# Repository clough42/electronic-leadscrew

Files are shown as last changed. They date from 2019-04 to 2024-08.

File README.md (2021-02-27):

# Clough42 Lathe Electronic Leadscrew Controller

This is the firmware for a lathe electronic leadscrew controller.  The goal is to replace the change
gears or gearbox on a metalworking lathe with a stepper motor controlled electronically based on an encoder on the
lathe spindle.  The electronic controller allows setting different virtual gear ratios for feeds and threading.

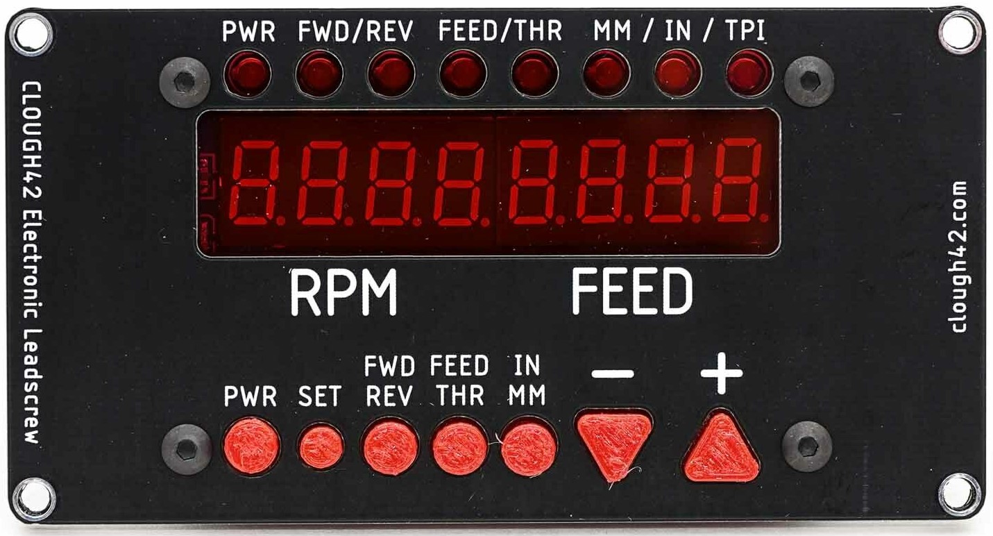
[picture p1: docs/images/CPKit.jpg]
Silkscreened Control Panel


## License and Disclaimer

This software is distributed under the terms of the MIT license.  Read the entire
license statement [here](https://github.com/clough42/electronic-leadscrew/blob/master/LICENSE).

**Machine tools can be dangerous.**  This is especially true of machine tools that can move by themselves
under the control of electronics and software.  You are responsible for your own safety.  Always assume
that something could fail and cause the machine to move unexpectedly.  Keep clear of pinch points and 
be ready to kill the power in an emergency.

## Latest Version

Version 1.4.00 adds the following features and fixes:
* Automatically detect if the ELS hits its max 100KHz step rate and fail safe
* Change the memory map to allow more thread and feed definitions

Version 1.3.01 added the following features and fixes:
* Fix phantom control panel button presses
* Add power button support
* Fix integer overflow for large metric threads
* Prevent mode and direction changes while running
* Smooth tachometer display
* Add support for lathes with separate feed and thread gearing

[DOWNLOAD HERE](https://github.com/clough42/electronic-leadscrew/releases)

## Project Status
Beta.

**NOTE: This is still a work in progress and is subject to change.  Hundreds of people all over the world have purchased parts
and built their own.  That's great!  I have had great success with mine, as have others.  Building an ELS
for your lathe does require require basic electronics and troubleshooting skills, so keep that in mind if you decide to build one
yourself.**

## Documentation
For documentation, please [**VISIT THE PROJECT WIKI**](https://github.com/clough42/electronic-leadscrew/wiki).

## Concept
The project is still in active development.  The current hardware looks like this:
* Use a TI F280049C Piccolo microcontroller on a LaunchXL prototyping board
* Use an inexpensive SPI "LED&Key" import display and keypad for the user interface
* Read the spindle position using a rotary encoder with a 3D-printed gear or belt drive
* Use a standard stepper motor (or servo) and driver on the lathe leadscrew
* Make as few modifications to the lathe as possible:
  * Use the original leadscrew and halfnuts without machining
  * Drive the leadscrew through the factory input shaft
  * Drive the encoder from the factory spindle gear train
  * Make it easy to restore the lathe to the original change gear configuration  

The ELS firmware currently supports the following:
* Feeds in thousandths of an inch per revolution
* Feeds in hundredths of a millimeter per revolution
* Imperial thread pitches (in threads-per-inch)
* Metric thread pitches (in millimeters)
* Imperial and Metric lead screws
* Support for powering down the leadscrew while leaving the tachometer active
* Tachometer averaging (stabilization)

Items on the short list for future development:
* Support for dual-shaft lathes that have different drive ratios for feeding and threading
* Leadscrew speed limit warnings

## Possible Future Goals
While this project is starting out as a simple gearbox replacement, some features seem attractive, even for
that simple case:
* Threading/feeding up to a hard shoulder with automatic stop
* Automatic recall and resync with hybrid threads (e.g. metric threads on an imperial leadscrew)

## Non-Goals
This is not a CNC project.  The goal is not to control the lathe automatically, but rather to transparently
replace the lathe change gears or quick-change gearbox with an electronic virtual gearbox that can be quickly
set to almost any ratio.  The lathe will continue to operate normally, with the operator closing and opening
the half-nuts to control feeding and threading.

## Hardware Configuration
If you want to get this running on your own LaunchXL-F280049C board, here are the settings you will need.
See the documentation at the link above for more details.

### Physical Switches
The LaunchXL-F280049C has a number of switches on the board to configure the GPIO and peripheral signal routing.
This provides lots of flexibility for different uses of the board, but it means that you will have to change
some of the switches from their defaults in order to use the GPIO pins and eQEP periperals.

These are the required switch settings
* `S3.1 = 0` Connects eQEP1 to J12
* `S3.2 = 0` Connects eQEP2 to J13
* `S4 = 1` Connects eQEP1 to J12
* `S9 = 1` (default) -- Connects GPIO32/33 to BoosterPack site 2 pins

S6 and S8 can be in any position.  0 is the default.

### External Connections
The firmware assumes the following pins are connected externally.

> NOTE: the silkscreen on the LaunchXL-F280049C board has the labels for J6 and J8
> swapped.  J6 is the header closest to the edge of the board.

#### Encoder
A quadrature encoder for the spindle is connected to the eQEP connector, J12.

#### Stepper Driver
A Step-direction stepper motor driver should be connected to the following GPIO pins:
* `GPIO0` (J8 pin 80) - Step
* `GPIO1` (J8 pin 79) - Direction
* `GPIO6` (J8 pin 78) - Enable
* `GPIO7` (J8 pin 77) - Alarm input

#### Control Panel
The LED&KEY control panel board **must be connected through a bidirectional level converter**, since
it is a 5V device, and the TI microcontroller is a 3.3V device.  A standard BSS138-based converter works
well.
* `GPIO24` (J6 pin 55) - DIO
* `GPIO32` (J8 pin 71) - CLK
* `GPIO33` (J6 pin 53) - STB (chip select)

#### Debugging Outputs
In addition to the control wires for the hardware, the firmware also outputs signals on two additional
GPIO pins to allow timing of the interrupt and loop routines.  An oscilloscope or logic analyzer may be
connected to these pins to debug and time the ISR routines:
* `GPIO2` (J8 pin 76) - Main state machine ISR
* `GPIO3` (J8 pin 75) - Secondary control panel loop

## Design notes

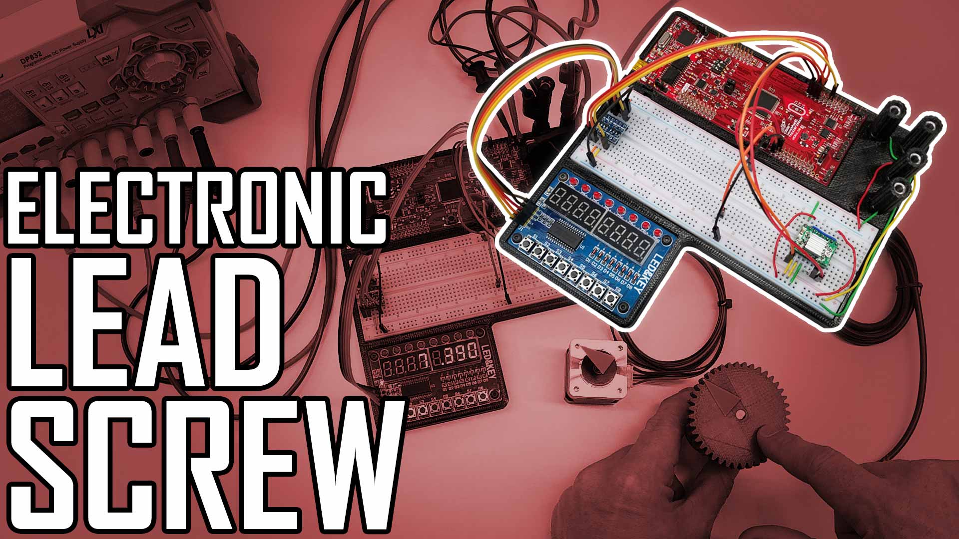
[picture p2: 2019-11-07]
docs/images/thumbnails/ELS - Part 1 - Proof of Concept.jpg

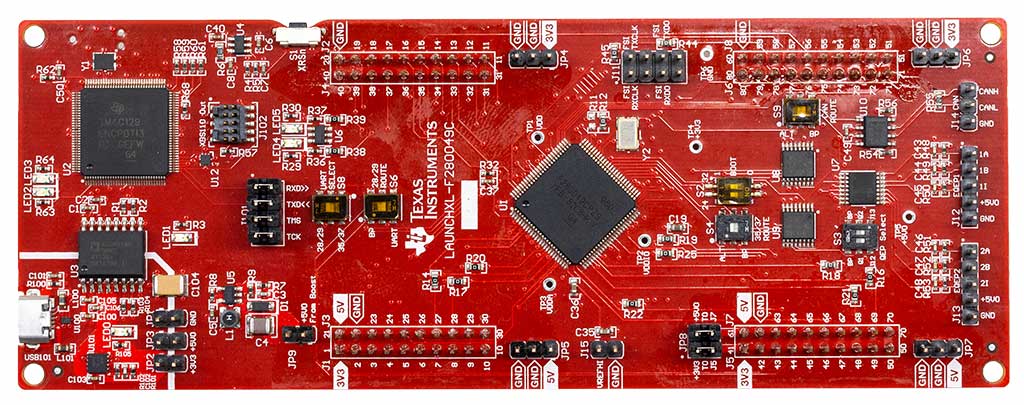
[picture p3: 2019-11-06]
docs/images/LaunchPad.jpg

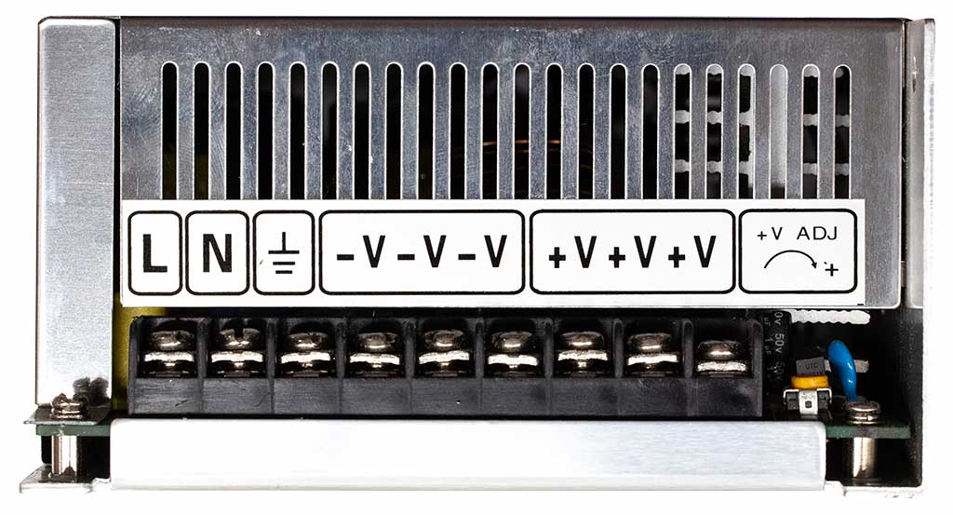
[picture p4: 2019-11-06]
docs/images/PowerSupply.jpg

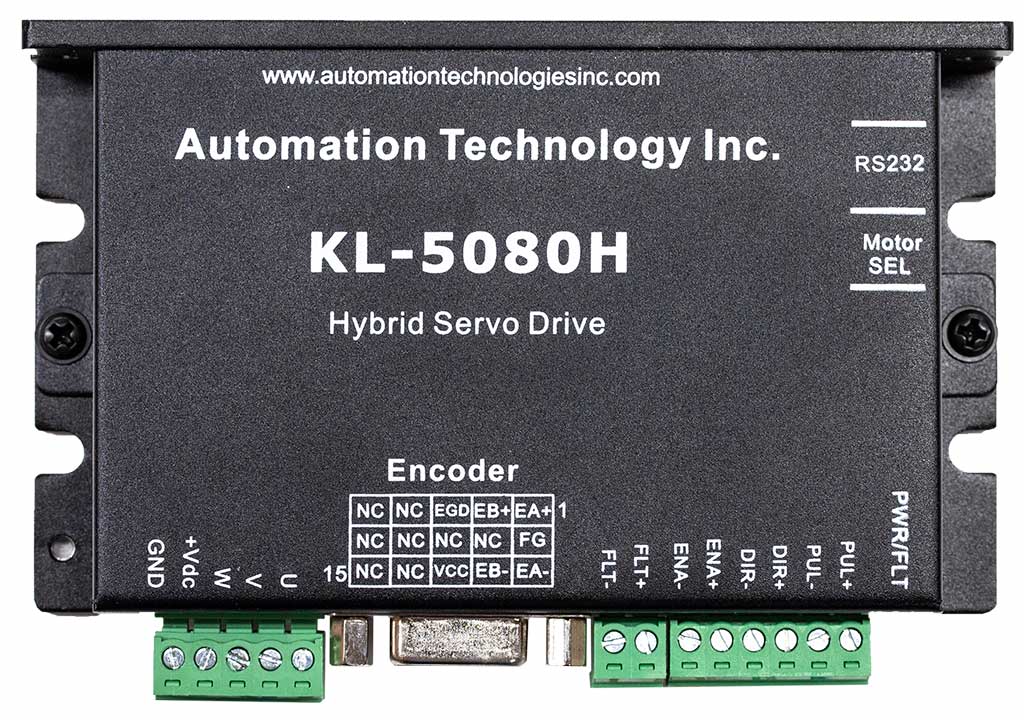
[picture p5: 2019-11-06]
docs/images/Driver.jpg

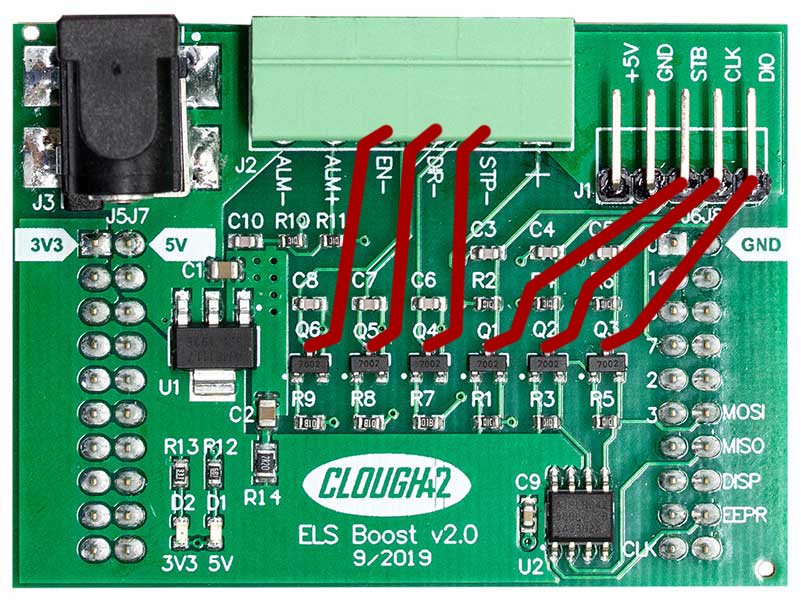
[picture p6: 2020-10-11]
docs/images/Continuity/ELSBoost-Output-Continuity.jpg

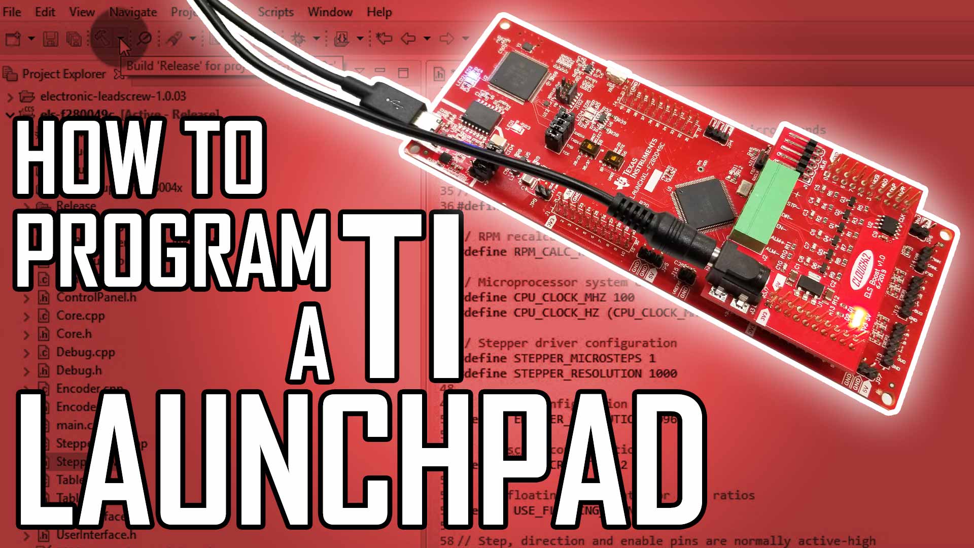
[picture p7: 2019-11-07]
docs/images/thumbnails/ELS - Part 10 - Programming the Microcontroller.jpg

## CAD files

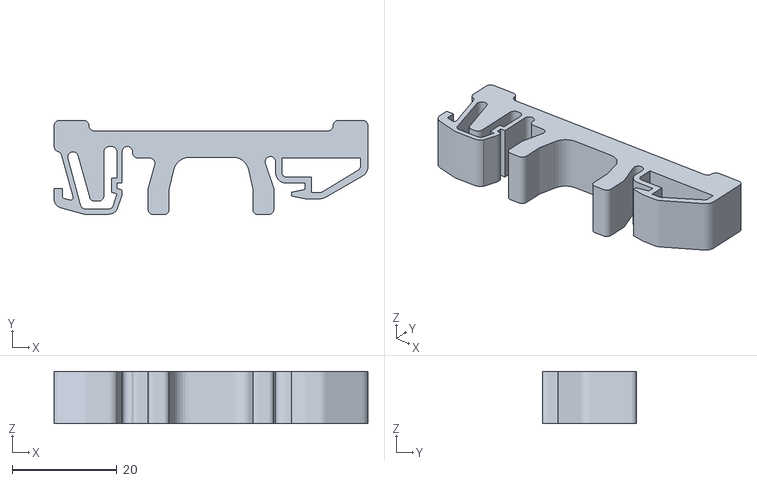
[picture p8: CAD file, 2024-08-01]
3D Models/LaunchPad DIN Rail Mount.stl
60.0 x 18.0 x 10.0

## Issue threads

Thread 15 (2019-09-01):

Configurable ratios for stepper / encoder pulleys / gears

gusosborne, 2019-09-01:
Hello,

Maybe I’m missing something simple again- but where would we configure the ratio for the pulleys (1:2 stepper driving lead screw, for example)? I would actually prefer to use gears in my setup, if at all possible. Would something more like a teeth setting ratio be possible (120:127 gears) to drive the leads screw?

I expect my encoder to be a 1:1, but curious if that configuration parameter exists (or will exist) as well?

Thank you again for this project! I’m pretty close to actually testing mine (especially if I can use gears;).

clough42, 2019-09-01:
I don't have configurable parameters for those ratios.  I just include them in the step and count values.

I have my servo driver set to 1000 steps per revolution, and the belt drive is 3:1.  For this setup, I set the steps value to:. 1000 * 3

I could also set it to 1000 and set the microsteps to 3.

I could add an additional numerator and denominator for each, but it's already pretty complicated, and I was trying to keep it simple.

gusosborne, 2019-09-01:
That all makes sense. Sounds like I can get what I need done, with some simple math as well then. Something like setting my steps to 1058.3 (assuming a decimal is allowed?), for my 120 driving 127 gears?

Is it important to set your steps to 1000 * 3 rather than 3000 for some reason ?

Thanks again.

clough42, 2019-09-01:
The math is done with whole numbers only to avoid representation issues inherent to floating point arithmetic.

I use 1000 x 3 just for clarity, so I'll remember what I did.

Why a 127-tooth gear?  That's usually used for metric/imperial conversion.

gusosborne, 2019-09-01:
It’s just the perfect size to be able to bury the stepper inside of the lathe, keep everything flush and hidden. I don’t have to do it that way, but I’d like to.

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

gusosborne, 2019-09-02:
I’ll just flip the bar around and try to use an idler then. I’m thinking this 2:1 (120 / 60 tooth) is going to be my best bet, using the stock gears. Then I can just configure my steps to 1000 * 2 (and you can close this thread;).

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

I was hoping to jam the encoder in between the ways (using a modified nylon 60 tooth) -  it would probably need some extra protection from oil and debris though.

gusosborne, 2019-09-13:
Freakin beautiful man!

LotusElan, 2019-09-13:
Thanks gusosborne.  This is how I handled the encoder.

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

J642, 2019-10-31:
Hi LotusElan The gears is it 40 tooth on both side. Jorgen

LotusElan, 2019-10-31:
The sprockets on the stepper and leadscrew are both 38 tooth and the ones on the encoder and spindle are 45 tooth.  So both are a 1:1 ratio. I based the encoder/spindle ones on what size would fit over the spindle shaft.  I think I based the stepper/leadscrew ones on what size I could make fit the leadscrew shaft.  I did have to machine 3 of the 4 pulleys to fit. Yes, the stepper is tucked inside the bed.  It didn't look like James had that option on his lathe.  Mine is in working order and I have used it but I can't wait to get a board for it so I can have a more polished install.

John

gusosborne, 2019-11-05:
Finally got back out to the shop today - happy with it so far. Now on to the encoder..

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

clough42, 2019-11-09:
Looking good!

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

Greecher, 2019-11-30:
As this seemed where the install showing where, here is mine.  First is my laser cut faceplate, second is showing how 3.3v straight through connection to TI board for display (no level shifter in place) works,  I think good brightness.  Next is power/servo controller  on the side of the cart that holds the lathe, last are internal mount of servo and encoder.  I think I'm pretty happy with the robustness of the 3d print that holds the servo in place, was able to re-use the banjo bolt holder and side cover bolt to secure it in place.

For the encoder I chose to use a double spaced bracket with skateboard bearings to support the pulley, as I didn't want to overstress the encoder bearings.  This was more necessary in my case, as when I pulled the old gear out and replaced it with a trimmed pulley (it is the same dimension pulley as attached to encoder, but trimmed down to just be the teeth, and a 3M 6mm width to match the dimension of the gear width I pulled out).  I may replace those 3d printed plates with aluminum, but for now it seems fairly steady.  Note I also used an alternate encoder that has a place to insert the end of the turned spindle that fits in the bearings and pulley center, so that it is more low profile.

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

gusosborne, 2019-11-30:
Awesome! I love seeing all the different ideas and implementations on these mounts.

J642, 2019-11-30:
It looks like my lathe and the set up I am trying to make. Awesome. I am
missing the interface board from James It came to Denmark but 150 mile from
my home. Ebay returned my money an I wait for a new batch of boards.

Den lør. 30. nov. 2019 kl. 14.45 skrev gusosborne <notifications@github.com
>:

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

Greecher, 2019-11-30:
> It looks like my lathe and the set up I am trying to make. Awesome. I am missing the interface board from James It came to Denmark but 150 mile from my home. Ebay returned my money an I wait for a new batch of boards. Den lør. 30. nov. 2019 kl. 14.45 skrev gusosborne <notifications@github.com
> […](#)
> : Awesome! I love seeing all the different ideas and implementations on these mounts. — You are receiving this because you commented. Reply to this email directly, view it on GitHub <#15?email_source=notifications&email_token=ANRWXG6N2PTVSLCCTXLMBETQWJU7DA5CNFSM4ISXGZY2YY3PNVWWK3TUL52HS4DFVREXG43VMVBW63LNMVXHJKTDN5WW2ZLOORPWSZGOEFQHKWY#issuecomment-559969627>, or unsubscribe <https://github.com/notifications/unsubscribe-auth/ANRWXG2UCAIWRIO7KWV6JN3QWJU7DANCNFSM4ISXGZYQ> .

As I chose to just power the TI board via the usb (which allows me to have programming access for updates), and just used 3.3V logic direct to the display board, I only had to build a small board for the 3 regular servo feeds (Resistor 1K, Capacitor 47pF, Mosfet 2N7000 for each) + alarm (2 resistor  10K, Capacitor 47pF).  James has a nice diagram for them in Circuit Maker, which I breadboarded first, then just made a small I think 12/12 hole perfboard.  Only thing I don't have is the support for the memory module, which depending upon software upgrades of ELS, I may either breadboard or purchase one of Jame's boards.

clough42, 2019-11-30:
Thanks for sharing your build.

Just for others that might read this, do not try to power the LaunchPad
board via USB (and the on-board 3.3V regulator) if you're using one of my
interface boards, or the 3.3V regulators will fight against each other.  I
honestly don't know what would happen, but I wouldn't recommend it.

James

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

Greecher, 2019-11-30:
> Thanks for sharing your build. Just for others that might read this, do not try to power the LaunchPad board via USB (and the on-board 3.3V regulator) if you're using one of my interface boards, or the 3.3V regulators will fight against each other. I honestly don't know what would happen, but I wouldn't recommend it. James
> […](#)
> On Sat, Nov 30, 2019 at 10:57 AM Greecher ***@***.***> wrote: It looks like my lathe and the set up I am trying to make. Awesome. I am missing the interface board from James It came to Denmark but 150 mile from my home. Ebay returned my money an I wait for a new batch of boards. Den lør. 30. nov. 2019 kl. 14.45 skrev gusosborne ***@***.*** … <#m_-5169150359964055550_> : Awesome! I love seeing all the different ideas and implementations on these mounts. — You are receiving this because you commented. Reply to this email directly, view it on GitHub <#15 <#15>?email_source=notifications&email_token=ANRWXG6N2PTVSLCCTXLMBETQWJU7DA5CNFSM4ISXGZY2YY3PNVWWK3TUL52HS4DFVREXG43VMVBW63LNMVXHJKTDN5WW2ZLOORPWSZGOEFQHKWY#issuecomment-559969627>, or unsubscribe https://github.com/notifications/unsubscribe-auth/ANRWXG2UCAIWRIO7KWV6JN3QWJU7DANCNFSM4ISXGZYQ . As I chose to just power the TI board via the usb (which allows me to have programming access for updates), and just used 3.3V logic direct to the display board, I only had to build a small board for the 3 regular servo feeds (Resistor 1K, Capacitor 47pF, Mosfet 2N7000 for each) + alarm (2 resistor 10K, Capacitor 47pF). James has a nice diagram for them in Circuit Maker, which I breadboarded first, then just made a small I think 12/12 hole perfboard. Only thing I don't have is the support for the memory module, which depending upon software upgrades of ELS, I may either breadboard or purchase one of Jame's boards. — You are receiving this because you commented. Reply to this email directly, view it on GitHub <#15?email_source=notifications&email_token=AAZLSHHUDALLY3HO2P2JGXLQWKSPTA5CNFSM4ISXGZY2YY3PNVWWK3TUL52HS4DFVREXG43VMVBW63LNMVXHJKTDN5WW2ZLOORPWSZGOEFQQAHY#issuecomment-560005151>, or unsubscribe <https://github.com/notifications/unsubscribe-auth/AAZLSHGTTA7UQJ4MBWXMKMLQWKSPTANCNFSM4ISXGZYQ> .

I would agree with this, it's fine for my one off, probably wonky results will ensue under double power.  Do note, I would still remove the jumpers and leave a cable in place, as if you are like me, I buttoned up my board in the back space, and didn't want to leave it open with the HV caps on the driver board for my lathe, so if you want upgrade access, you can still do so without cracking it open.

Dave

clough42, 2019-11-30:
One other thought...

If you're running the board off a 5V supply through USB, the 3.3V supply is
provided by the TPS79601DRBR regulator on the LaunchXL board.  You'll want
to keep an eye on the current draw and temperature to make sure you don't
run into trouble down the road--especially if your installation is in a
space that gets hot.

James

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

carneeki, 2019-12-14:
I just had a thought for the mounting of the stepper. I have a CQ6125x550 which is a metric variant of the G0602. If you're fine with direct drive, then the gearbox could be removed, and a new bearing block + stepper bracket could be fastened to the casting where the gearbox used to go. Finish up with a new sheet metal cover and the control box and VFD knob can be put on something nicely etched and look factory fitted :)

(I realise it's a lot more work but I see it as one of those "how long is a piece of string?" type questions as to how far one wants to take this)

Closed 2020-10-11.

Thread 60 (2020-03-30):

Gearbox ratio

Vrossi050, 2020-03-30:
Still having gearbox ratio issue.  See photo.
 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

Closed 2020-03-30.

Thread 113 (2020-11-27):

ELS functional logic appeared to work...display flickered for a while, now dead

TreatHull, 2020-11-27:
When first hooked up, the control panel was DOA - no sign of life in any regard.

After tracing, tracing and tracing again, I found that the ground wasn't connecting with the control panel. When I tested the cable (an old VGA cable), the ground lead was open.

After several efforts to troubleshoot, I got to a place where when I powered up the unit, one red LED illuminated on the control board....but nothing else happened.

I carefully made up a new cable to connect the control panel only 12" long to minimize noise and when I powered up - the control panel was sort of working. The alpha-numeric display was seemed very dim and flickering quickly, but I could make out Clough42 and the version number.

After the bootup information was done, the RPM showed zero unless I spun the encorder, when it produced plausible RPM just like it was supposed to, except so dim and flickering it was almost impossible to see.

Likewise, when I pressed the up and down buttons for feed, the value in the feed screen went up and down like it was supposed to. However it was also so dim and flickering that it was almost impossible to see.

While this was going on, several of the red LEDs at the top of the control panel were lit up. LED's 1 and 2 were brightly lit, while LEDs 4 and 7 were lit but not as brightly. (See image below. The numerals look quite bright in this image, but they are actually fickering on and off very quickly making them appear dim.) 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

I broke out my 100MHz Rigol dual channel oscilliscope, but had to do some reading (and watching youtube videos) to try to understand how  the control panel worked and what stb, clk and dio were supposed to be doing.

When I fired things up again with the scope attached to stb and clk, it didn't look right (see screen images below with blue trace = stb and yellow trace = clk). If I understand correctly, it's sort of working correctly: when stb goes low, the clk turns on.

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

However, I expected to find more 'binary' voltage values, either 5 vdc or 0. Instead, there are intermediate voltages that showed up and also what looked like noise.

Update: December 13th, 2020

In order to keep up momentum, I switched my focus from the display to installing all the components in my Hammond steel cabinet (which took a lot longer than I expected). When I powered it up, the servo/hybrid stepper appear to work fine, but now no more digits on the control panel, just a red LED at the left end of the board.

I checked continuity from on end to the other, but everything checked out fine, so I figured the problem has to be at the level of one of the boards. I ordered another TI Launchpad, a Clough42 booster board and an LED & KEY board. While waiting for them to arrive, I figured I could test the existing LED & KEY board by using an Arduino to power it and see if I couldn't get the display to light up.

I tried two different Arduino sketches (programs) to drive the TM 1638 LED & KEY board but ... nada! I double-checked the pinouts for each one and they were fine. The waveforms on my scope looked fine, but there's no way I could make the segments light up. This suggests that the LED & KEY board is at least part of the problem, if not the whole problem. I'll know more once the replacement board gets here sometime in 2021.

Update  December 16th

The new Launchpad arrived from Digi-Key in just over a day. I removed the jumpers, set the switches and wired it in last night. The encoder drove the hybrid stepper correctly but the LED & KEY Board was still dead.

To try and understand why the board was dead (except for one red LED which showed it had power), I hooked up the oscilliscope again.

Even though the control panel didn’t function, the signals being passed to the control panel were more ‘healthy’ looking.

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

Channel 1 above shows the STB while Channel 2 shows CLK. As it’s supposed to, when STB goes low, CLK is activated.

The waveforms are a lot closer to what I expected, but I still wound up with some unanswered questions. Let me start with the questions I had on the screen capture above. The vertical scale for both channels is 2.00 volts/division. Examination shows that the delta between high/low for the STB line is closer to 2 volts than the 5 I expected. Does it matter? if so, what could be causing this? Does it matter?

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

In the second image above Channel 1 shows STB while channel 2 shows DIO. When STB goes low, commands or data are sent on DIO.

The y-axis scale for both lines is still 2 volts/division. What caught my attention in the display was the waveform on DIO (blue) where halfway through the wave train, the lower voltage level increased by a volt giving a 4 volt delta between high and low. I had the same question here: does it matter? And if so, what could be causing it.

At the current pace, I may actually learn something by the time the new display board arrives from China in the new year.

Incidentally, in case it helps someone else, I found a YouTube tutorial on the operation of the TM 1638 display which really helped me understand what was going on: [https://youtu.be/KxfhVqne1Qs](https://youtu.be/KxfhVqne1Qs) You can ignore the Arduino code and just focus on the communications protocol for the display if you want to.

I should have the Clough49 booster board delivered next, followed by the new LED & KEY board sometime in January (!). One board down, two to go.

Update December 25th

The Clough42 Booster Board arrived a few days ago. I soldered the required bits and pieces, tested for continuity from the pins on the board to the display (all good) and powered it up. No display, except for the red LED on the board. With two out of three boards replaced and no joy yet, it's highly suggestive that it's the display board. Further testing may have to wait on the arrival of the slow boat from China.

stahlous, 2020-12-27:
I had similar issues with flickering on my LED & KEY board. I had very reasonable `signal voltages on my oscilloscope with the LED & KEY board disconnected, but they went to heck when I reconnected it. I figured I screwed up the soldering when I removed the straighter header pins to connect the supplied 90deg header pins. Turns out that was the issue -- after I re-soldered all the connections it runs solidly. I figure I probably had a whisker of solder nearly shorting out +5V to GND.

TreatHull, 2020-12-31:
December 31st update:

Thanks to @stahlous, one problem solved.

I went back and examined the solder job I did on the header and I must have been really careless when I de-solder and removed the old header because a bit of the copper via was lifted and torn away from the Vcc pin. Other parts of the board were getting power, but the torn via appears to have cut off the supply voltage to the TM1638. No wonder nothing was happening.

I did a real kludge repair which involved a blob of solder on the end of a piece of #24 wire and then hooked it up to my Arduino, but still nothing happened.

As I checked the sketch (program) for the Arduino, I finally noticed that the pin assignment for the output pins was wrong in the code I copied online. One minute correcting and uploading the sketch and -bingo- the control panel lit up at full brightness, no flickering and worked the way it was supposed to with the little Arduino test program.

When I switched cables and connected the control panel to the ELS, the control panel was dead once again.

When I hooked up the scope, I found that the STB and CLK waveforms were good, but that the voltage difference from high to low was only about 2.5 volts:

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

However, when I put the scope on STB and DIO, I got a different result. The voltage swing on DIO was just over 5 volts - what you'd expect, while STB was still only about 2.5 volts.

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

I got the same waveforms with and without the control panel connected.

So now (1) the control panel works correctly with signal input from my Arduino which is progress; and (2) I trying to figure out what would limit the high-low voltage swing on STB and CLK, but not DIO.

JonWoellhaf, 2021-01-01:
I suggest you carefully check the switch settings and jumper configuration on the TI board. Good luck!

forrestlw, 2021-01-01:
It appears that he is using a Arduino board. I didn't respond because the Clough42 project it based on a TI board.  "I tried two different Arduino sketches (programs) to drive the TM 1638 LED & KEY board "

TreatHull, 2021-01-01:
@forrestlw  Sorry if I wasn't clear in my explanation. The ELS uses the same components as James at Clough42: a TI Launchpad, the Clough42 booster board and a TM 1638 control panel from Clough42.

The Ardunio board was only used to test whether the TM 1638 control panel was functioning correctly, which it was.

TreatHull, 2021-01-09:
Hurray!! The slow boat from China arrived this week and my new control panel board was delivered.

Connected it up, fired up the system....and it works perfectly.

The problem was a bum control panel board, probably due to my rough-handling the removal of the original header and installing the new one.

Even before I hook it up to the lathe, I want to say that this has been a terrific project. This is a hobby that I pursuit to have fun and learned new things. Though it required some patience, I had fun and I learned buckets, one of the most rewarding projects I've done in long time.  I encourage anyone else who's considering it to give it a go.

Couldn't have done it without the excellent videos and components from Clough42 and the advice received. Spec thanks to @stahlous who hit the nail on the head. Thanks all!!

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

Closed 2021-01-09.

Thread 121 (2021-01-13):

Someone please help, it just wont run.

xfuzz, 2021-01-13:
Please help me figure this out
I have it all together assembled for testing. Servo wont spin. It gets energized so I can't turn by hand when powered. All the led's light up on the TI and boost boards.  The control pannel lights up.when I spin the omron encoder the rpm's  show up on the control panel. The buttons show changes with each push ,  but servo does not spin. I have triple checked continuity all good. I am perty sure all dip switches are set correct as well. I tried going to the older version software 9.1 to up load the els software too. One thing when doing so is I do not get the red  pause break point icon on the TI  software like Jame's does in his videos. It just seems to complete to upload without stopping no break with red icon. The servo & encoder are from Automation Tech. The number on the encoder is different it is ES-D508 , servo is ES- M32320S. I called as when I received them,  I ordered same as the ones James used. They told me they are exactly the same and numbered for a different market. I am lost. One  more thing,  I purchased my Launchpad  directly from TI , it did not have the tape  on the dip switches like James video. Not sure what that means.  **_I have uploaded pictures of the wiring below_**

mac651955, 2021-01-17:
Mine didn’t work when I initially set it up.  Flip the switches on the micro processor back and forth a couple times to make sure they make contact.  Additionally go ahead and make all your connectors up and use them as your problem may be in connections.

xfuzz, 2021-01-17:
Thanks for 5hevinout. I tried the switch flipping multiple times M I red all the post and someone suggested it prior to you. I have continuity on all of the connections. The servo is getting power as I stated if I flip one of the two dip switches on the servo encoder it will rotate back and forth one revolution non stop. It's  something simple , but what?

mac651955, 2021-01-17:
Are you using the servo encoder combo that James used or something different.  If it is the same double check your three leads from the servo to the servo controller.  Make sure they are correctly connected U, V, W. You might be getting your phases working against each other.

xfuzz, 2021-01-17:
Yes. As I indicated above  according to Automation tech it isi identical. . I will have to find the schematic,  I have have brown on "U", blue on "V", black on " W", I think that is correct.

xfuzz, 2021-01-27:
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

xfuzz, 2021-01-27:
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

JonWoellhaf, 2021-01-27:
Do you have the Pro_Tuner, hardware, and software manuals for your ES-D508?

If not, you can download them from https://mecheltron.com/en/product/es-d508.

I think you will need all three manuals.

Do you have an oscilloscope?

Your connections from James' Boost Board to the ES-D508 should be as shown at the top of page 8 of the hardware manual. The boost board has a "sinking" type output.

Do you have a jumper from pin 1 of the driver connector to pins 3 and 5 of that connector? In the photo, it looks like you do, but I want to be sure.

candera, 2021-01-27:
I'm actually having a similar problem (see #125), and am no expert, so take the following for what it's worth, which is "not much".

I took a long look at the pictures you posted, and I can't see anything wrong. You've checked continuity, and it sounds like when you flip DIP switch #2 it runs the self test, which seems to indicate that the motor is running. The only things I can think of are either that continuity is not actually good or that there's a lot of noise in the system. But with noise you'd expect some movement, even if random.

The critical pin for you is the STP- pin. If ENA- were not pulled low, the motor wouldn't be energized. And DIR- doesn't really matter - whether it's high or low the motor is still going to turn, it's just which direction. Unfortunately it's a little hard to test, since in order to turn the motor it needs to go high and low a bunch of times. I did try wiring a pushbutton switch between ground on the TI board and the STP- pin so that I could press it a bunch of times and generate a pulse train. I even tied the ENA- and DIR- pins low to try to take out any variables. I *think* that was a good test (maybe someone else can tell me why it's a bad idea) so perhaps you could replicate it. If pushing the button doesn't rotate the motor at all then perhaps it is a motor controller problem. Iit might take a lot of pushes, since if you're configured for, say, 800 microsteps per revolution, each push is only going to move it like a third of a degree.

In my case, I believe perhaps the motor is bad, as I can get at best random movement from it. I've ordered a stepper to replace it. Hopefully I'll have more luck with that. The hybrid servo concept is very cool, though - I really wanted it to work, so I sort of hope it's just a bad motor rather than some weird thing with my setup.

xfuzz, 2021-01-27:
Jon et me start with a huge thank you for your assistance i downloaded the manuals. Not sure what I am looking at. I do not have an oscilloscope.Yes all the positives are connected via a jumper wire from one to the other two. Continuity on all, I do not have the required cable to enter data to the encoder. I will order one right away if that is what I need.  Actually I don't know a sinking output from one  that is not. I can follow instructions though.

mac651955, 2021-01-27:
In the photos it appears that (if you used the same wire colors as the encoder) your encoder is wired wrong.  The first pin from the bottom is 0v common and you have what appears to be the blue wire going to it.  Also you have 6 connections on your plug and that is a five pin header.  Check your wiring then maybe try a five pin connectors.

xfuzz, 2021-01-27:
Mac I triple checked and blue is marked common the omron. i up loaded pic. the 6 spot on the connector is  empty

JonWoellhaf, 2021-01-27:
xfuzz,

OK, let's see if I can help you get this working. Troubleshooting would be much easier if you had an oscilloscope. Can you borrow one?

Candera (above) offered some good information. I'd like to simplify the problem as much as possible.

First though, I think it's important you understand the schematic at the top of page 8 in the driver's hardware manual. Do you?

xfuzz, 2021-01-27:
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

xfuzz, 2021-01-27:
I would not how how to use one ,  have no one to borrow from. I uploaded more pics of the wiring I think I do understand page 8.

mac651955, 2021-01-27:
Did your server come with the signal cable, if it did are you using it.  Just covering all bases.

xfuzz, 2021-01-27:
Mac yes it did I am using it

xfuzz, 2021-01-27:
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

JonWoellhaf, 2021-01-27:
OK.
I am confused by the statement at the top of page 8. It reads, "For the enable signal, apply 0V between ENA+ and ENA- or leave them unconnected to enable the drive." If left unconnected, the LED in the drive's opto isolator will be off. I would expect that to be interpreted as disabled, but the text says off is enabled. I expect the sense of this input can be changed in the software.

So please try this:
1) Power off.
2) Disconnect the ENA- wire from pin 6 of the driver. Tape its end or attach a wire nut so it doesn't short against something.
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
xfuzz, 2021-01-28:
ok going t try

candera, 2021-01-28:
Yeah, I tried that. Pulled enable and direction lines to ground, then wired ground to PUL- via a switch. Clicked it a ton of times. No movement.

One thing I noticed is that the driver I got differs from the one in the picture on the eBay listing. So I'm sort of wondering if they ran out of stock of the thing I ordered, grabbed a return off the shelf and ditched it on me. :p

My new motor arrived this morning. Driver arrives later today. That at least should tell me whether it's the motor or something else. My power supply is kind of suspect, too, so we'll see.

xfuzz, 2021-01-28:
here is how I set it up
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

xfuzz, 2021-01-28:
meter
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

xfuzz, 2021-01-28:
ok i am using my drill to spin omron. spinning at 1000rpm i get 77.2 no spin i get52 to 56.on meter

xfuzz, 2021-01-28:
changed setting on meter it now reads no spin 61.2-68.4. spinning at 1ooorpm it reads 99.8-100.4mv

JonWoellhaf, 2021-01-28:
I don't see my latest comment. I wonder if it got lost in the aether. I wrote:

OK. It looks to me that your TI board is working. If it wasn't pulsing you'd see no change in voltage.

I think either the driver, motor, or encoder is defective. Sorry. Can you get a replacement?

If you want to send me just the TI board, boost board, and control panel, I'll check them out.

xfuzz, 2021-01-28:
OK. ill pack them up and send those items. Thanks.

xfuzz, 2021-01-28:
I doubt it is the omron as it sends rpms to the control panel. the control panel seems ok as well as it displays all button pushes and rpm. logic implys the TI, or servo encoder and servo itself. Thoughts?

JonWoellhaf, 2021-01-28:
I meant the encoder on the servo motor. I think your spindle encoder is fine.

xfuzz, 2021-01-28:
ok just so I am clear,send the servo encoder{ES-D508) the TI and boost board?

JonWoellhaf, 2021-01-28:
Just the TI board, the boost board, and your control panel.

xfuzz, 2021-01-28:
Got it

JonWoellhaf, 2021-01-28:
Don't send the ES-D508, motor, or power supply.

JonWoellhaf, 2021-01-28:
Did you try it with enable and direction open?

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

candera, 2021-01-29:
So, good news. My new motor arrived today, and when I wired it up it seemed
to work perfectly right out of the gate. I got a stepper instead of a servo
so I might try again, but looks like I just got a bum motor!

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

xfuzz, 2021-01-29:
Jon, I mailed it this morning. I enclosed a return pre paid label. use it for the return trip home. thanks

JonWoellhaf, 2021-01-29:
OK. I’ll let you know as soon as it arrives.

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

xfuzz, 2021-02-02:
It seems the package is on a sight seeing trip. It was sent 2 day priority,  gotta love the USPS
February 1, 2021, 4:11 pm
Departed USPS Regional Facility
SOUTHERN ME DISTRIBUTION CENTER
Your item departed our USPS facility in SOUTHERN ME DISTRIBUTION CENTER on February 1, 2021 at 4:11 pm. The item is currently in transit to the destination.
January 31, 2021, 12:53 am
Arrived at USPS Regional Facility
SOUTHERN ME DISTRIBUTION CENTER
January 30, 2021
In Transit to Next Facility
January 29, 2021, 5:11 pm
Arrived at USPS Regional Origin Facility
DETROIT MI NETWORK DISTRIBUTION CENTER
January 29, 2021, 11:03 am
USPS in possession of item
ROSEVILLE, MI 48066
January 28, 2021
Pre-Shipment Info Sent to USPS, USPS Awaiting Item

xfuzz, 2021-02-06:
FINALLY! USpS says it was delivered. So glad I sent it Priority.  Let me know what you think.

JonWoellhaf, 2021-02-06:
I think a guy reenacting the Mormon immigration put it in his handcart and walked it across the plains!

Looking at it now.

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

JonWoellhaf, 2021-02-06:
SOLVED! (I think). Check your private messages on Practical Machinist.

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

candera, 2021-02-06:
I'm curious. What was it?

xfuzz, 2021-02-11:
A unsoldered pin. Jon discovered it and fixed it. Runs perfict now.

candera, 2021-02-11:
Awesome, glad you got it working. I've been chipping away at the other hard problem: how to attach everything to the lathe!

xfuzz, 2021-02-12:
Do you have access to a 3d printer?. Check thinigieverse.com there are
several stl files of mounts and gears search clough42 and els to find the
files.

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

candera, 2021-02-12:
I do have a 3D printer, and I've already printed a bunch of pulleys. I even printed a belt in flexible filament. So I'm not stuck or anything: just working my way through the process. :)

Closed 2021-02-11.

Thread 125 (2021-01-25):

Problems driving hybrid servo motor using James's kit

candera, 2021-01-25:
Posting this here because I'm not sure where else to go and I'm a bit stuck.

I've been working on getting the Electronic Leadscrew set up using James's kit. I've got the display working after a bunch of dumb mistakes (whoops plugged the boost board into the wrong set of headers), and when I spin the encoder it shows a reasonable RPM, so I think that's working as well.

What I can't get working is the hybrid servo motor I'm using. I've triple-checked all the wires are correct and continuity is good. But when I spin the encoder the motor just sort of stutters and doesn't do much. Sometimes it turns a bit, but it's definitely not doing what it's supposed to.

I've got some basic electronics knowledge, but I'm pretty new to motor control. I've never used a hybrid servo before. I bought this one: https://www.ebay.com/vod/FetchOrderDetails?itemid=124061452016&transid=2351269567002&ul_noapp=true

I've tried every combination of DIP switches and inverting the drive pins I can think of. I've got it wired the way James' instructions suggest, with +5V to the PUL+, ENA+, and DIR+, and the STP-, EN-, and DIR- outputs of the boost board to the corresponding inputs on the motor driver. I *think* perhaps there's something up with that, though, because when I put a logic analyzer on the pins, it shows a boatload of noise. Like, even if I'm not spinning the encoder I'm seeing lots of high/low and low/high transitions on the step and direction lines.

At one point I was able to get a clean signal on the logic analyzer, where I'd see pulse trains on STP- like I'd expect, including the direction line flipping appropriately. I can't quite remember at this point what I was doing, though. I may have been measuring the pins with all the outputs inverted.

So I wonder if I should be driving it differently? Like, should I be driving the PUL+ pin instead of the PUL- one? Again, totally new to motors. Sorry I can't put my question more intelligently - I'm a n00b. Any input would be extremely appreciated.

xfuzz, 2021-01-26:
I too am having trouble getting the servo to spin. I requested help here too. There is this one fellow Jon  who seems to be very knowledgeable and has helped others but has not committed on my post as of yet. I am praying he is well and will chime in. James has not commented in some time. I follow his channel and he is busy with his new mill. Maybe he will look and take pity on us. Good luck sorry I have no clue how to help you.

candera, 2021-01-26:
Right now I can't tell if it's noise or a bad motor. The logic analyzer seems to show a clean signal when I separate the cables, but it might be triggering on a level that's wrong for what the motor controller is expecting. There is certainly plenty of noise when I measure with the cables in close proximity. I don't have an oscilloscope to see what the signal actually looks like. My next step is to wire up a simple motor driver to test the motor in isolation so I can tell whether it's the control signal or the motor itself.

xfuzz, 2021-01-26:
I have no clue how to do any of that. I am thinking it is the ti launchpad itself or the servo encoder as everything else seems to be ok.  I'll give it a few more weeks to see if anyone sqn help me figure it out . If not I'll try to sell what I have to recoup some money and just use myntaps and dies a usual.

candera, 2021-01-26:
Well, I'm pretty clueless myself, but if you want to give any more details on the problem you're having I can maybe throw some ideas your way.

xfuzz, 2021-01-26:
Thanks I appreciate any ideas. I believe I covered everything in item #1.1 just a few post below. Nothing has changed in my setup. I think it might be something simple but no idea what that might be.

candera, 2021-01-26:
Can you post a picture of your setup, particularly the hookups to the motor controller?

xfuzz, 2021-01-26:
Well sure if I knew how. I tried to do that in my original post but couldn't figure how to. I even looked in the get hub help section.
I got you replys in a email maybe I can reply with attachment pics. I'll try now.

xfuzz, 2021-01-27:
I sent a reply via email with pictures. I don't see it here in gethub. So I have no idea if you received it.

xfuzz, 2021-01-27:
The file came back to large. I just sent 3 separate ones mayb that will get to you

candera, 2021-01-27:
Does not seem like it came through. That's a shame. I'm sure it's quite frustrating - I know computers quite well and I'm fairly frustrated with this project at this point.

For my part, I've ordered a new motor. A bit expensive but I think I can still return the old one if it turns out the new one works out. And if not, well, I guess maybe it's the power supply?

xfuzz, 2021-01-27:
Damn the bad luck. I sent several with one pic each to cut down on the
size. I know they can be posted on get hub just cant figure out how. I am
feeling very ignorant now. I do wish to thank you for the time you gave me.
Hope you get your working soon.

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

xfuzz, 2021-01-27:
Got the uploaded with a little help they are on under open items #121

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

xfuzz, 2021-01-29:
Did the new servo and encoder work for you?

candera, 2021-01-29:
I wound up buying a stepper instead of a servo. Arrived today. Hooked it up and it worked perfectly straightaway. Definitely a bad motor or bad driver. Given the weird behavior, my money is on the servo encoder being bad. Anyway the new motor works a treat. Hopefully I can return the bad one.

I may still try to pick up a hybrid servo at some point, since I like the concept and I have some other projects I want to do, but a stepper should work fine for me and I've got it all hooked up.

xfuzz, 2021-01-29:
Congratulations! Good to hear. I am sending my ti board to Jon so he can
test it. That should narrow the search for a solution.

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

JonWoellhaf, 2021-01-29:
It seems several people have had trouble with the hybrid servos, but not with the steppers. Is there something simple we’re missing? If you can’t return the bad stuff, I’d love to examine it.

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

candera, 2021-01-29:
Unfortunately I have a somewhat limited window to return it. Otherwise I'd be totally game for sending it your way.

There's a pretty good chance I will pick up another one as part of another project I have in mind, though. I'll try to remember to report back here on whether it works. If not, we can see about analyzing it.

Thanks a ton for all your help with this. I thought I was going bonkers, having tried everything I could think of. I'm glad it was just a bad motor, but it really helped me not feel so out in left field when I was troubleshooting.

Closed 2021-01-29.

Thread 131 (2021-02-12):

Encoder Problem?

JPL-Dx, 2021-02-12:
Trying to install the ELS on a 14 X 30 Hendey Lathe.
Per bench test, everything with the ELS Controller seems to work except the RPM display.
Spinning the encoder shaft does not change anything.
Stepper Servo Driver is powered up without any faults.
The servo motor is locked with power on, can be spun with power off.
I have completed all suggested trouble shooting and  looked through all posted issues hoping for enlightenment, all without success.
 Continuity Checks all OK
 Voltage Checks all OK
 Wiring Checks all OK

I tested my encoder using an LED and all channels seem to be generating a pulse.

This should be simple, what am I missing?

Stumped!

mac651955, 2021-02-17:
Double check your dip switch settings first.  Flip them back and forth several times.  Second double check your solder connections.  Connection issues seem to be the root cause of the problem you are encountering.

JPL-Dx, 2021-02-19:
Thanks for the suggestions. My encoder is no good.  Checked it with a scope and discovered the output signal is under 1 volt.  That is not high enough to trigger anything.  I have another one on order.  I am pretty sure that will solve my problem.  Waiting on delivery.

JPL-Dx, 2021-03-08:
Finally received the new encoder. Hooked it up and it works as expected. Next step is to install on the lathe.

Closed 2021-03-08.

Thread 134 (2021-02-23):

Waiting to solve with ELS, I need a  momentary solution to power-feeding

andrea271068, 2021-02-23:
Hi, I have a question, if for this moment I wan to use the servo to run just the leadscrew for power feeding what I should do? I need just to buy a simple pulse generator with forward and reverse? Or I need to buy also other stuff, Arduino etc.  Can somebody list to me what I should buy for my servo? I wan a simple momentary solution, at least I can power feeding and use my lathe. I don't wan to disassemble the ELS set up and put back gears.
I bought a nema 23 hybrid servo for the Clought42 automatic lead-screw project.

IS NOT MY SURRENDER!!!

clough42, 2021-02-24:
There are lots of published arduino projects to speed control a stepper motor and there are also stepper speed control devices available on eBay.  I've never worked with any of them, but they might provide a solution for you.

andrea271068, 2021-02-24:
But this is not what i'm looking for in truth I really wan to solve my ELS problems, dis you read about  my problem? I flesh the code LounchXl (I had sever problems but not look like ia working) but look like that  cannot communicate to display.
I bought again a new PCB and led&key to check again with a new pair.
Can you help me to solve? I'm little lost, there are one gentle persons that is trying hard ti help me there, without him I' lost in this issue. Please can you check to my story?

Closed 2021-02-24.

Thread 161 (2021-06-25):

RPM and direction issue

maxjenius, 2021-06-25:
Hello, I'm having an issue where my spindle is running at 300 RPM, but the panel says its going 1400 RPM or thereabouts, no matter the steps or microsteps I use (also tried different encoder counts).  RPM changes as I change the spindle speed.  The servo runs fine, speeds up and slows down as it should, but trying to use REV, it spins the same direction.  Connecting to the driver through serial, I can spin it either direction just fine.  I just can't figure out why...all my connections are correct and continuity for everything is good.  Anyone see this problem?

maxjenius, 2021-06-27:
Update:  Downgraded to 1.3.0.1 and back.  This fixed the RPM issue, but still cannot get the leadscrew to run in reverse....odd.

JonWoellhaf, 2021-06-27:
In James' project Wiki at <https://github.com/clough42/electronic-leadscrew/wiki/Continuity-Checks> he details how to check end-to-end continuity by probing board pads. Have you tried that for the DIR line? I found one board that had an unsoldered pin that didn't make contact with the pad. This process can also diagnose a defective solder joint.

Do you have an oscilloscope, or access to one?

maxjenius, 2021-06-28:
Thank you so much for helping!  Yes sir, I went over that section and checked all lines for continuity:  they all passed.  I do have a scope, what should I probe and look for?

JonWoellhaf, 2021-06-28:
Are you able to probe the boost board while your lathe is running?

maxjenius, 2021-06-28:
Sure thing.

JonWoellhaf, 2021-06-28:
OK. Please try this:
1) In the Wiki article, scroll down to the Output Pins section and locate transistor Q5, then find it on the board.
2) Set your lathe to run at a couple hundred rpm.
3) Ground your scope lead and probe Q5's top terminal. It should be either 0 or about 5 volts.
4) Stop the lathe.
5) Push the FWD/REV button. (In the latest software, FWD/REV is inactive when the lathe is running.)
6) Verify the panel FWD/REV LEDs swapped.
7) Start the lathe.
The voltage should be the opposite of what it was before.
If it isn't opposite, probe either end of R8 (below Q5) and make the same test.
Let us know what you see.

maxjenius, 2021-06-28:
OK, so I probed the top of Q5 while the lathe was running...I get 0V in either FWD or REV (LEDS swap fine).  Probing R8 resister gives me 3.3V in FWD and OV in REV!  The transistor the issue?

JonWoellhaf, 2021-06-28:
It sure looks like Q5 is bad. Sorry.
It's a long shot, but probe the left-hand bottom lead of Q5 and see if the voltage changes.
If it does, then it's pretty certain Q5 is bad.
If the voltage doesn't change at the left lead of Q5, but DOES change at the left end of R8, then it's an open in the very short board trace between the two.
Another thought: Can you examine the board around Q5 with a 10x loupe? Compare the connections and components around Q4 and Q6 with those around Q5. All three should look identical.

JonWoellhaf, 2021-06-28:
I just had another thought.
It may be that the DIR output is shorted to ground somewhere.
To check this,
1) Power off.
2) Remove the wire from the DIR pin on the driver connector.
3) Measure the resistance between ground and the connector screw.
I get an open circuit.

maxjenius, 2021-06-28:
OK, confirmed everything.  Left bottom lead of Q5 changes along with R8.  No shorts detected when testing as you suggested.  Inspecting with a loope looks good, traces are all identical.  Looks like a bad Q5, which is good since I can easily replace it.  I'll check my spare parts bin to see if I have a 7002 transistor and swap it out.  I'll report back.

JonWoellhaf, 2021-06-28:
OK. It's great that you can replace Q5!
I thought of one last test to confirm Q5 is bad.
1) Remove the driver wire from DIR on the driver connector.
2) On the driver connector, put a resistor (1K to 10K or so) between +5 and DIR.
2) Probe DIR and see if stays at 0 volts when you do the test.

maxjenius, 2021-06-28:
I ended up replacing Q5 before I saw your last message.  Looks like you nailed it, everything works now.  Thank you so much Jon for the help, I never would have suspected that component.  Time to make some screws!

JonWoellhaf, 2021-06-28:
Excellent! A bad transistor was about the last suspect on my list, because they're usually so reliable -- unless you let the magic smoke out, of course. Did you see any physical damage? I'm delighted you got it working. I haven't heard of another bad transistor on one of James' Boost boards.

James, if you're listening, did you find any bad ones during your board testing?

maxjenius, 2021-06-29:
No physical damage at all, board was pristine.  I was not handling it while grounded though, so it may have been my fault.  I've built plenty of boards without, but hey, it does happen.  Thanks again for the help!

Closed 2021-06-28.

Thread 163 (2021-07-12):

Programming launchHXL

GrayOneAus, 2021-07-12:
Hi James
Have recieved your Electronic lead screw control panel and ELS Boost board v 2.1
So followed your very good youtube on how to program the board (current version of ccs_setup 9.3)
All seemed to go well (brand new laptop no programs loaded) tried debug mode program loaded (ver 1.3) latest
However the only thing the control did was to light up ie all leds on and display showing 7 and the rest are 8's buttons do not respond. no error reported by the loader.
Have gone through all your board tests and double checked all the connections all appear to be OK all power light are as they should be. (only have the launchHXL and control panel connected as per the youtube leads are 4" long only change I made to the config file was to make it metric at 300 for 3mm pitch
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
Would you have any idears as to the problem ? Not sure how to run the debugger to see the out put to the control panel Oh all switches on board have been changed as discribed (s3 and s4 also 1,2,3 are disconnected)

clough42, 2021-07-12:
That is really odd.  Usually, it either works completely or doesn't work at
all.  Have you checked continuity using the instructions on the GitHub wiki?

Does the display change at all if you press any of the buttons?

On Sun, Jul 11, 2021 at 10:57 PM GrayOneAus ***@***.***>
wrote:

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

GrayOneAus, 2021-07-12:
Yes I have gone through all the instructions (all check out as required)
No the display does not change when you press the buttons.

I believe it is some where in the programing that I have not got right (like other programmers did you have to load a driver for the display?) It would be nice if you could do a youtube on how the debugger works as you explain things very well
Oh yes changed the connections to screen cable to see if that was an issue, no change still the same problem.

GrayOneAus, 2021-07-14:
Hi James
Re above have watched your Youtube a number if times, and suddenly relised
The led 5 is flashing on my TL LaunchPad after pressing the run key in the debugger.
It does not in your youtube. does this give you a clue as to what is wrong with my setup!

GrayOneAus, 2021-07-20:
Hi James
Finally got it working!
It was that nasty Code composer (getting your version was real hard kept getting some sort of corruption) any way after trying the third computer  finally it clicked.
Just awaiting the for the encoder to arrive to try the next part.

clough42, 2021-07-20:
Awesome!  Glad you got it working.

James

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

GrayOneAus, 2021-07-22:
Hi James
Can finally report that the unit works on the bench, (having just recieved the rotary encoder).

One comment I would make, see attached pic cables would be better off in protected flexable conduit may also help with screening.

And finally you need a DRO on your lathe (would make a good project, and yes I have one fitted make turning a breeze)
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
Keep up the great Youtube stuff

clough42, 2021-07-22:
The flex shield is a good tip.  It'll work best if you connect the shield
to the chassis ground at one end only.

James

On Wed, Jul 21, 2021 at 10:21 PM GrayOneAus ***@***.***>
wrote:

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

Closed 2021-07-22.

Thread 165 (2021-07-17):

Power Feed not using half nuts

BL-Shopwork, 2021-07-17:
Another Clough42 ELS up and running! Thank you James for putting this together in a great video series and how to. I am running the "Clearpath-Killer" you recently posted, its working great.

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

I managed to tuck the Servo and encoder into the head below and above the ways. next up is mounting the interface on the front.
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

Feature I would like to put into the code:
I am fortunate to have a Power feed carriage and I prefer not to use the half nut unless specifically threading. My carriage has a 2:1 reduction for this power feed. I would like to have the "Feed" mode of the ELS  change feedrate on an additional 2:1 reduction. When in "Thread" mode it will for obvious reasons run without the additional gearing.
**UPDATE:** Solved this with hardware. I installed a NC momentary button for the feed stop that is wired to Pul+/Dir+. Now when the carriage hits the feed stop, the servo stops, this of course is NOT for threading.

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

(PLEASE let me know if this has already been done by one you fine folks, hate to re-invent if not needed)

dsgroninger, 2021-07-17:
BL,

It's really easy to set up for separate feed rates if your carriage has a gearbox feed.  My Precision Matthews 1030 has this setup, and it's just one or two lines of code to change in configuration.h.  Here's a writeup that I did on my implementation.  There's a page in there on configuration.h changes and the math that I used to figure out my settings.
[Clough42 Electronic Leadscrew.pdf](https://github.com/clough42/electronic-leadscrew/files/6835349/Clough42.Electronic.Leadscrew.pdf)

Good luck,

Dan

BL-Shopwork, 2021-07-26:
Thanks for the writeup Dan, I don't know how I missed that line of code regarding feed micro stepping but it did exactly what I needed. For me I had to double the micro step value and its working great.

With respect to the feed stop I started down a path that was turning overly complex (for what I was trying to do). I was trying to setup new inputs to disable via software, then a magnetic switch to trigger said input and around I went for the past week until I just decided to put a simple NC momentary limit switch (button) in series with the Step/Dir + wire from the launchpad breakout to the servo...... Maybe not the most elegant, but its works really well.

Now when the limit is hit, the servo stops dead. Simple, effective and super easy. I also put a switch in parallel to the feed stop switch so that I can disable the feature for example when threading or its just not needed.

SoManyHobbies, 2021-07-27:
I was curious if anyone had run into cases where the ratio between the half nut and power feed couldn't be accounted for by just adjusting the STEPPER_MICROSTEPS_FEED and STEPPER_RESOLUTION_FEED values?
I have a PM 1228 lathe and have been struggling to figure out how to account for the difference in power feed rate.

I've got an 8 TPI lead screw, and the 180W Integrated Servo, and plan to use a 6:1 ratio (3:1 motor to lead screw input, and 2:1 in the gear box similar to how Cough42 had his setup in his video).

I'm using a STEPPER_RESOLUTION value of 1000, and STEPPER_MICROSTEPS of 6.

However the problem comes in with the carriage power feed. If, for example, I have the gear box set to thread 16 TPI (0.0625 in/rev), that same gear box setting would drive the carriage 0.0072 in/rev. Which if expressed as a ratio of (thread feed)/(power feed) would be 1/0.1152, or if "reduced" to the smallest whole values is 625/72.

Maybe I'm just thinking about it all wrong, but I don't see how I can set the STEPPER_MICROSTEPS_FEED and STEPPER_RESOLUTION_FEED to account for a difference like that.

I am comfortable writing in C++ so if there are any suggestions of a change I could make to use a different calculation when in feed mode I am willing to give it a shot.

dsgroninger, 2021-07-27:
SoMany,

Please look up two items in this thread where I linked to my writeup on my implementation on a PM1030.  It deals with exactly the situation that you have in using the separate gear ratio of the carriage feed rather than the half nut for feed.  For the 1030, I think the gearbox ratio was 3.33:1, so the math worked out to round integers for me.  I think that if you find this line in configuration.h:
#define STEPPER_MICROSTEPS_FEED

and set that to twice what his line is set to:
#define STEPPER_MICROSTEPS 3

If that's 6 for you and the threading feed is correct, then set STEPPER_MICROSTEPS_FEED to 12.
#define STEPPER_MICROSTEPS 6
#define STEPPER_MICROSTEPS_FEED 12

Anyway, I have the lines of configuration.h that I changed listed in my writeup.

Good luck!

Dan

SoManyHobbies, 2021-07-27:
I did read through your writeup, and it was really helpful. But I think the part that I got hung up on was that the ratio in my case didn't work out so nicely to result in whole numbers.

I do have STEPPER_MICROSTEPS set to 6 currently.
But if I understand things correctly setting STEPPER_MICROSTEPS_FEED would basically double the feed per rev when in feed mode. But in my case the power feed rate isn't half the threading feed rate, it's closer to 8 times slower (8.680555555......) to be more precise.

If I did just assume it was 8x, I could set STEPPER_MICROSTEPS_FEED to 48 (ie. 6 x 8). If my math is right that would result in a difference of about 8% between the calculated feed rate and true feed rate. Probably not a big deal at low feed rates, but might become a concern at higher feed rates.

Does that seem right, or am I just making this too complicated? :)

dsgroninger, 2021-07-27:
Wow, 8.68:1 seems like a lot.  I spent a lot of time turning the lead screw by hand and watching feed motion on the DRO to come to my measurement of 3.33:1 on the PM1030.

If it really is 8.68, then if your threading micro steps are 6, then 8.68 x 6 = 52.08.  For feeding, what's it matter if the rate is just slightly off?  Set STEPPER_MICROSTEPS_FEED to 52 and you're only off by less than 0.2%.

Now, the only problem with all this is that at high spindle RPMs, you're going to exceed the 100 kHz limit on clocking the stepper controller.  James has the code set up to trip out if the clock to the stepper goes above 100 kHz.  For me, it's more  of a problem at high feed rates, but the rates are higher than I'd try with a lathe like the 1030 anyway.  I have the math around that in my writeup too.  I'd expect you to hit that limit at 0.040" per turn at 1/5.2 of what I did, so something like 180 RPM.  If that's a problem, I'd change the stepper controller to use fewer pulses per revolution, maybe 300 or 500 rather than 1000 pulses per rev.  There's a couple of places to play with settings to trade off where one hits that 100 kHz.

SoManyHobbies, 2021-07-27:
Good point about setting MICROSTEPS_FEED to 52, I think I was hung up on it being an even multiple of the thread feed because I was actually defining it as
#define STEPPER_MICROSTEPS_FEED STEPPER_MICROSTEPS * 9, but makes more sense just to set it to 52 and put in a comment about where the number came from.

Yeah, I am really worried about running out of spindle RPM as well as the 100 kHz limit. I may actually decide to set the gearbox different between threading and power feed. If I max out the feed the gearbox can provide I can get up to 0.0115 in/rev, which puts the ratio at 5.43... Which isn't quite so bad, but you're right I may end up needing to drop the steps/rev count on the motor in order to support feeding at higher RPM even if I change the gearbox between the two operations.
I might even add some code to flash the gearbox setting on the display for a few seconds when changing from feed to thread and vice-versa.

Initially I came up with the ratio just using the threading/feed chart on the lathe, but I did validate with and indicator and manually rotating the spindle and measuring the movement.

SoManyHobbies, 2021-07-28:
Thank dsgroninger for the help. I think using the existing mechanism might work well enough even for odd ball gear boxes like the one on my PM 1228.

But one suggestion I might have would be to possibly include the option to just set a floating point value that is a ratio of power feed to threading feed. So we could plug in values like 8.6805, and assume it is then a multiplier to the existing feed rate. Then if we carry that value until as late as possible in the calculation it might help minimize rounding errors.
Note:
- This assumes we are in the #ifdef USE_FLOATING_POINT case
- This would replace STEPPER_MICROSTEPS_FEED and STEPPER_RESOLUTION_FEED. I dunno which one would be more useful to others.

Seems like the feedRatio() function in Core.h might be a good candidate since it's already treating its product as a float?

But I don't fully understand the math well enough to know if it would work or not. Or if it's worth keeping this issue open for such a change. I didn't intend to hijack the OPs issue if the original issue has been resolved.

BL-Shopwork, 2021-08-03:
Solved with code edit to change feed rate Microsteps, hardware feedstop used.

Closed 2021-08-03.

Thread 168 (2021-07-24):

Did I fry my Launchpad

IamTomzo, 2021-07-24:
Greetings - I apologize if Github is not the right place for this sort of inquiry.   I can't find the right forum for Clough42 ELS communications.

I got everything soldered up, did the continuity checks, and connected it to my Win10 PC.   The device was recognized, but after I loaded the code it stopped being recognized.  I tried disconnecting the Clough42 board and reconnecting the jumpers to use just USB power to see if the board was recognized but no luck.

I was pretty careful about static, although I must admit that I was not using my antistatic mat and wristbands - even though James said he fried one - duh.

Anyway, if anyone has any tips about these boards not being recognized I am all ears.

JonWoellhaf, 2021-07-24:
When you plug the USB connector into the TI board, does the computer beep? Are you sure the other end of the cable is still plugged into the computer?

IamTomzo, 2021-07-24:
It recognized the board at first and had the requisite beep.  The code seemed to load - it went through all the steps.    I have done a lot of arduino projects so I am familiar with editing config.h files and the like.   I tried different cables, checked the device manager, etc, but windows says there is a hardware problem.   I failed to take proper static precautions (stupidly) so it looks like TI is going to get another $30 from me...

clough42, 2021-07-24:
When I fried mine, it was a connection issue with the power pins, causing
5VDC to end up on the 3.3V power rail.

I would suggest checking all of your support joints and testing the boost
interface board by itself, not connected to the new LaunchPad to make sure
the 5 and 3.3v supply pins are correct before you begin.

Also, remember that the three power jumpers on the LaunchPad board must be
in place of you're just connecting USB for testing, and off if you're
providing power through the booster pack board.

If you are powering through the booster pack, you can still program through
USB with the power jumpers off.

James

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

IamTomzo, 2021-07-24:
Thanks James (and BTW this project and your channel area awesome).  I did take off the power jumpers before sending 5V through your board although to test things out I also removed your board and reinstalled them to see if it would work.  No change.

I got both of the lights (3.3 and 5V) on your board and all the continuity checks were good.   Are you saying I should measure the voltage as well?  If there was a solder bridge across the 3.3 and 5V pins on your board would both lights still light up?

I did notice one LED on the TI board that was on before it fried and then was off.  It was either LED4 or LED5 (I did not note this when it was on but noticed it was off when things were not working).  Reading the documentation from TI those are not power LEDs but are related to GPIO 23 and 34 and the only pin that this project uses was 34 (if I am reading the documentation correctly).   I am spitballing here so forgive me - I should have taken more careful notes when I was doing all of this but excitement got in the way.   When I powered it up the PC recognized it and connected.   After I loaded the code is when it failed.   Could I have wired something wrong so that the code sent power the wrong way?

I have another TI board on the way - they are cheap and TI does 2 day shipping, so my weekend will be freed up for some honeydos (which will please my wife) so all is not lost.   Heck - I don't even own a lathe (yet) but love projects like this.  I figured that when I do get my lathe it will either be off Craigslist or a Chinese import - either way it is getting torn down for cleaning, etc and I want to install this as things go back together.

Thanks for all you do!

clough42, 2021-07-28:
Yeah, I would definitely check the voltages of the 5v and 3.3v supplies
with the boost board disconnected from the launchpad.  If there is a bridge
or a damaged regulator, the 3.3v might output 5v, and that would kill the
launchpad.  The 3.3v led would still light, but would be brighter.

Also be sure the three power jumpers are of the launchpad before powering
it through the boost board.

James

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

IamTomzo, 2021-07-28:
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
Thanks James - I powered up your board and measured 5.21V and 3.34V across the 5V and 3.3V pins (red oval in this image) using the ground pin in the green circle so that seems OK.  The pins on the display connector are reading 5.21V.  Are there other pins to measure or does this mean the board is OK?

Of course, it could be that my observations earlier were flawed and I killed the board through a lack of static protection.   The $30 for the new board is not as bad as having to wait to get the next one, so I don't really want to brick another one...

IamTomzo, 2021-07-28:
And by the way, I realize this is not your day job and you have better things to do with your time.   My replacement launchpad should arrive today so I will give it another go - with better safeguards for static and better control/documentation of conditions - and see how that goes.

clough42, 2021-07-28:
That looks good to me.

James

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

IamTomzo, 2021-07-28:
Thanks.   Again, I appreciate what you do for us hobbyists.   BTW, you have also inspired me to drop some of the COVID weight that added to the other extra weight I already had when it started.  No fads - just watching calories and moving more.  Down about 15 pounds so far with another 40 or so to go!

clough42, 2021-07-28:
Awesome!  It's all about making a choice and taking control.

James

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

IamTomzo, 2021-08-02:
It's alive!!  Finally managed to get this done properly without letting any of the magic smoke out.   I am converting an old desktop PC case into an ELS electronics enclosure.   Still need to finish all my cables, but the tips on the wire termination tools was super helpful.  I am using the StepperOnline integrated servo, so I need to figure out the precise settings on that, but seeing that I don't quite have a lathe yet, I am going to do all the final software configuration once I know my reductions, etc.   I am leaning toward the G0602 but the ire from my wife for dropping $2500 on another one of my "toys" is the main obstacle.   She already has to deal with ~$10K worth of gear in my observatory....
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

IamTomzo, 2021-08-07:
Well, since this last post I took the project from the desktop and installed it in my enclosure.   I think I failed to set the boost board properly - it appears to have been set on only one row of the pins which could move 5V onto the 3V section.   Result - another dead TI board - UGH.

As I waited for my new board to arrive (oddly TI would not let me add a third one in two weeks to my cart so I had to buy from Mouser), I rechecked all the continuity tests and tested the cables through the enclosure all the way to each device.   All were in the right places.   However, I still have something wrong going on.

I carefully removed the jumpers and set the switches in full anti static mode (anti static mat, wristband, etc).   I then made sure the boost board was set properly this time and went to load the firmware.   I used the TI supplied USB cable and just a light in the area right next to the USB connection lit up which is what was expected.   I then plugged in 5V power to the boost board and nothing.   The TI board was not recognized by the PC.   I then took off the boost board, reset the 5V jumpers so I had just a bare TI board and connected via USB and presto - the board comes alive and can be flashed.   This is odd because it is the same boost board used in the image above.

Anyway, after I flashed the TI board I took it back out and installed it into my enclosure with the boost board.   When I powered everything up the display flickered a bit followed by a POP and the familiar smell.   I immediately powered down and upon inspection the TM1638 chip had fried.  This is the same display board pictured above, so it had worked previously.   I stripped the TI board down, reset the 5V jumpers and it still connects to the PC, so it does not look like I fried that board (again).

I have another of the LED&KEY boards on order but was wondering if any of you have any thoughts on (a) why the TI board won't connect to the PC when using power from the boost board and (b) what error on my part would cause me to fry the display?

Thanks

Tom

IamTomzo, 2021-08-10:
OK - I got the new LED&Key board and the one I received this time was clearly made better than the last two - even though I got them from the same source.   Odd.   I also noticed that I fried the voltage regulator on the boost board so I ordered a 10 pack of those and replaced it successfully.   I have everything in the enclosure and it powers up fine to the Clough boot screen but I am getting nothing from my encoder as RPM on the display.  Consequently, the servo does not spin of course.   I tested the encoder with an ohmmeter (black/blue, blue/white) and they read the same so I am pretty sure the encoder is OK.  I flipped the switches back and forth a few times to make sure they were set correctly on the TI board.

I also tried both of the encoder connections EQEP 1 and 2 (and reflashed the code accordingly) same result.   I do not have an oscilloscope to do more detailed tests on the board, but in reading a closed post here on github from another user it may be the TI board (again).   Are there any good tests that can be done without a scope?  If there is a bad resistor can I just get one and solder it onto the board rather than buying a whole new board?

Also, on a side note, I used a laser thermometer to look at the temps on the boost board just to see what was going on there.   The only thing that stood out to me were resistors R7 and R8 which seemed warmer than the rest heating up to ~125F pretty quickly.   Not sure if this means anything but it is a data point.

Thanks

Tom

IamTomzo, 2021-08-19:
I got it figured out - and posted a video on my "need help wiring Clearpath Killer" issue.   As always I was the problem but want to thank all of you who helped me out.

clough42, 2021-08-19:
I saw your previous message saying R7 and R8 were getting warm.  Do you
know what was causing that?  They're connected to the gates of MOSFET
transistors, so they should only carry brief spikes of current at 5mA max
during level transitions.

James

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

IamTomzo, 2021-08-19:
I am not sure but it might be the fact that I had 12V going through there due to my stupidity.   When I was building my enclosure I bought a 12V and a 5V wall wart.  I guess I must have had another 12V on my workbench (I power stuff in my observatory on 12V regularly) and I actually printed a label that said 5V and put it on the wrong wall wart.   It got installed into the enclosure and I only realized it when I was troubleshooting the encoder and found 12V on pin A.   I am quite embarrassed by the mistake, but that goes for nearly all of my mistakes.

I just fired it up and checked with my laser thermometer and they are all running just a hair above ambient temperature.   I suppose that temperature increase should have made me check that power supply earlier, but hindsight is always 20-20.

The real question is when I get to buy a Clough42 T-shirt!   Thanks for all you do!

Closed 2021-08-19.

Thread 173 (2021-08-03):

Need help wiring the "Clearpath killer" -  iSV57T-180

IamTomzo, 2021-08-03:
Greetings,
Inspired by James' testing of the integrated servo that cost only $100 I bought one but can't seem to figure out exactly how to wire that motor up.  I realize that the enable pin will not be used, but I am not sure how to deal with the DIR + connection on the motor.  I have read through the documentation to the extent of my ability and tried to zoom in and see how James wired it in the video, but don't want to let any more magic smoke out as I complete this project.  He appears to have some of the pins jumped in the video but it is hard to tell.

The only possible matches I can find are:
STP -> PUL-
"+" -> PUL+
DIR- -> DIR-
ALM+ -> ALM+
ALM- -> ALM-

I may be way off here. Has anyone else wired this up (well, I know James did)?  If you would be so kind, could you give me some information on the correct way to wire this?  One image is from the manual showing the connections and the other is the Clough 42 board.

Thanks

Tom
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
.
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

IamTomzo, 2021-08-03:
Doing a bit more reading I see that the jumper that I see in James' video appears to be connecting PUL+ to DIR+ according to this chart from the manual for the motor.   Of course, it could also be going from PUL- to DIR-, depending on which of these diagrams is chosen.  I would just try each of them but don't want to fry anything.

Also, there are inline resistors in this diagram but I don't see anything like that in any of the documentation from the wiring schematics - perhaps those are already on the boost board.  I see some on the board and perhaps that is their function, but I am unsure.

I apologize for my glaring lack of knowledge in this area, but that is one reason I took on this project as by doing these things I always learn a few things.

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

BL-Shopwork, 2021-08-03:
+        -->   PUL+ and Dir+ (orange with red jumper in photo below)
STP-   -->   PUL - (White)
DIR-   -->   DIR- (Blue)

Not using Alarm
36v power supply for my setup.

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

I set my microstep dip switches S1,2,3 for 1600, did not change the stiffness (70).

IamTomzo, 2021-08-03:
Awesome - thanks!   That is just what I needed to know!  I may just wire up the ALM connectors anyway - I suppose it could not hurt.

IamTomzo, 2021-08-04:
Of course, even though I had the board flashed and working with the display, when I got it all into the enclosure it seems that I have fried another TI board.   SMH.   I sounded out all my connections again and all of the continuity checks come out perfect.   Not sure where I went wrong this time, but I have a third TI board on the way.

IamTomzo, 2021-08-19:
First off I want to thank all of you who took time out of your day to help me along the way.   As usual, the problems I had were entirely self inflicted, but three dead TI boards later I got it working on the fourth!  I also want to thank James for all his work on this very interesting project.   I don't even own a lathe yet (coming soon) but the project was too cool to pass up!   Here is a video showing how I cobbled it together in an old desktop PC case.

Thanks again!

Tom

https://youtu.be/JKiJtWTBcc0

Closed 2021-08-19.

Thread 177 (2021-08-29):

ACT Nema 23 Hybrid Stepper behaves like a impact driver

eglische, 2021-08-29:
Hello!

I've played around now for the better part of 2 days. I came to a point where i could get a smooth action when i used the absolute minimal feed. But everything higher, or even a standard metric 0.75 thread and the stepper motor is hammering away, like crazy. it stalls out at maximum and below a bit of that of course without load, no mater the rpm, even on sub 150rpm on the spindle, it sounds like the little guy grinds away something.

At the moment, there are two things i think is important for troubleshooting, the micro step stetting, and the fact that i use a 4:1 shaft output for the encoder, and a cheap encoder i had laying around, giving me much less resolution of course. BUT the RPM is correct (verified with a tachometer), it's stable and it seams ok.

Steps settings: (giving me 4800 steps for a 3:2 Reduction to the 3mm Lead screw comes out to a 3200 s/r on the lead screw)
`#define STEPPER_MICROSTEPS 8
#define STEPPER_RESOLUTION 600`

Encoder Resolution (yes it is low.... got the wrong encoder, new one is on it's way)
`#define ENCODER_RESOLUTION 30`

**The setup as is accurate within reason. IE. the Encoder translates the correct values and advances the carriage the correct amount per spindle revolution**

Things i tried:
- up the voltage from 36v as per specs to 60v as maximum permissible, change the power supply out
- reducing the steps to full step, half step quarter. (it's a 200s/r@1.8° stepper, it's set now to 16 micro steps effectively, the lowest i would go). The idea of going 1/16 now was, i hoped to get it smoother - nope.
- checking the wiring of course
- checked the coils, got 0.9-1ohm = correspond with other steppers i got working good

Things i am going to try later on:
- setup the stepper as a 4th axies on my mill to see if mach3 gives a smoother step train of signals to verify the stepper is not the cooperate.

If someone has a idea, i am glad for any input.
Thanks

eglische, 2021-08-29:
one note on the side: stepper behaves that way even with no load attached, so it's not that it's too weak or anything....

eglische, 2021-08-29:
i hooked it up to my cnc and configured the stepper driver and the stepper as a 4th axis, it runs perfectly well and smooth and has a lot of force, so i have to exclude that possibility and i suspect the signal train coming from the launchpad is choppy/faulty.

at this point, i am out of my water and need help if i want to conclude this project :(

clough42, 2021-08-29:
Yeah, the encoder resolution is *way* too low.  The ELS firmware doesn't do
any time interpolation between encoder pulses.  It depends on having the
encoder pulses arrive nearly as fast (or faster) than the required output
steps.  With such a low-resolution encoder, it's getting one pulse from the
encoder and trying to generate a large burst of steps to catch up to where
it now thinks it needs to be.  The results are as you observe.

With small discrepancies, it isn't a big deal, because the micro-stepping
absorbs the small bursts of steps.

James

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

eglische, 2021-08-30:
Good Morning and Thank you :-)

Yes, i was afraid so. Have ordered a used 2000p and a "standard" new 1024p.
Guess i have to gear up the output as well now. to get near that sync ratio (1600 Pulses / 1mm feed Rev) Or/and Go down with the micro stepping.

After sleeping on it, and your confirmation on that, i think this issue can be closed.
Thanks again James

Cheers
Roger

Closed 2021-08-30.

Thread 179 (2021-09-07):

ELS. Every thing connected up and looking good but motor refuses to turn. Looking for Help Please.

smbab7203, 2021-09-07:
Newbie From UK.
Hello to you all.
 First and foremost I must say a huge thank you to James for all his hard work in the production of his youtube channel. I have been following the ELS project with great interest for quite some time now. I have taken the plunge and ordered all the parts.
I have read all the issues on this project and have learned a great deal from all your collective knowledge, so a big thank you to you all.
I have very little electronic/electrical knowledge so I am hoping you can help me with my current problem. No pun intended.
Motor and controller is.
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
When I power everything up, drive looks ok no alarm LED.
The LED & KEY board looks ok, the buttons all work and when the encoder is turned by hand the read out showws the speed which I assume is correct.

When the spindle encoder is turned the motor does not turn. Thats the rub!!
I have no scope so can only check connections with a multimeter. So please forgive my lack of knowledge.

The driver is Stepperonline CL86T.  -- If I check between the following connections on the drive with my meter I get the following results when spinning the encoder by hand.

ENA - &  ENA+     On meter no change   0v.
DIR - &   DIR +     On Meter   1.3v  and 5.2v this changes depending on direction.
PUL - & PUL +      On Meter   1.3v   No change at all. Change direction no change.
ALM + & ALM -    On Meter    3.3v

FYI. I have purchased a cheap motor frequency driver from ebay, when connected this drives the motor smoothly with no obvious problems. so I am assuming the motor and driver are not the problem?

Any help or suggestions you guys can give me as a way to resolve this problem will be much appreciated and gratfully received.

Kind Regards and Thanks in anticipation.
Steve B.

Turner75, 2021-09-07:
Oldie, originally from UK, now in Hawaii.
Sounds like no enable signal or clock pulses getting to drive. Encoder
output and buttons being processed by Ti launchPad so..... Check enable and
pulse on the interface boost board o/ps. Also the switches s3, s4 and s9
are set correctly.  The soldered connections on the boost board could be
the problem. My dim vision and shaky hand made soldering the connectors a
little tricky!
 I find that a led in series with a 4.7K resistor on flying leads can be
useful and spot many a fault that a DVM gives ambiguous readings.
 I found o/c diode on LED&KEY from Clough42 kit using the simple led tester.
 Cheers Graham

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

smbab7203, 2021-09-07:
Hi Graham,
Thank you for your prompt reply.
I am not exactly clear what you mean, just to be absolutly clear are you saying:- connect the LED in series with the 4.7k resistor. Then connect that in the lead running to the pin you want to check? so if the pin is carrying a signal it will light the LED?

FYI. I have purchased a spare interface board from James because I made a school boy error when soldering the LED&Key board so ordered a spare for both boards because of cost and carrage from US to UK. anyway I might just solder it up and solder a LED resistor tester as well.
Is there a specific way to solder the resistor to the LED because the LED,s are pos / neg sensitive i believe ?
I will dig out some LED,s and resistors tomorrow and have a go. I will let you know what i find.
Thanks again.
Regards  Steve.

Turner75, 2021-09-07:
HI
Sorry I was not too specific about the led/resistor test lamp
configuration. The led, being a Light Emitting DIODE is sensitive which way
round it is connected into the circuit being tested. Does not matter which
end the resistor is connected to the led but I have a  black, negative,
lead  to the led cathode, usually the lead out of the led next to the flat
on the body, and the resistor to the anode, positive, of the led with a red
lead connected to the other end of the resistor, i,e, everything wired in a
series loop.
To use, connect the black lead to the zero, 0 volt terminal on the board
and red lead  is used to poke around looking for positive volts, led will
light if the testing point finds a  positive voltage above the turn on
voltage of the diode, which is usually around 1.5 volts for a red led. If
the level is 3 volts, the led will be some what dimmer. If the test point
is pulsing, i,e, the clock or output of the encoder, then the brightness
will be less. The clock or pulse line to the stepper drive has very short
pulses which at low rev. settings may be difficult to see in normal
lighting, depending on your drive input requirements, pulsing high or
pulsing low.
Sorry the explanation is so long winded but l don't know your level of
electronic experience and I have tried to cover the very basics. Somebody
may reply that reverse connecting the led will damage it, I have not seen
that happen at the low, 5 & 3 volt levels found in these logic circuits
with a limiting resistor of 4700 ohms. This device is meant for logic
levels only, upto 5 volts max.
Cheers Graham.

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

smbab7203, 2021-09-08:
Hi Graham.
Thanks for another detailed reply.
Just a little back ground info. I have recently retired after working as a service engineer on CNC Machine Tools. I was biased towards the mechanical side of things mainly. The company thought was if your happy doing electrical work fine. When you get stuck shout help and they would send an electronics engineer to help. Consiquently my knowledge of electrics/ electronics is  limited. So dont apologise for a lenghthy reply, the more information I get from you the less chance I have of messing things up. If I am unsure about anything I will Ask.
Anyway, I have sent for some resistors and leds. Please bear with me for a couple of days for delivery  and I will get on the case and let you know what I find.
Thanks again for your understanding.
Talk to you soon.

Regards   Steve.

Turner75, 2021-09-08:
HI Steve
The Github link does not support long emails. Tried sending a page or two
of background++a pic. or two, machinery of course. No success, bounced back.
Have you a regular email address?
Cheers Graham

Turner75, 2021-09-09:
---------- Forwarded message ---------
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

smbab7203, 2021-09-09:
Hi Graham.
How are you doing? I hope all is fine with you (In the sweet spot on planet Earth) !!
I borrowed some resistors and Leds from a mates son's science project.
I built the tester. I am getting signals from the spindle encoder but signals going to the motordriver don't seem to change. Unless they are too quick for the LED to follow? The only one I can see change is when I spin the encoder in different direction which to me is correct?
From my limited knowledge I think the Clough interface board is playing up. I am going to solder up the new one later this evening and will give that a try. Watch this space.
I really appreciate you taking the time and trouble to help me. Thank you again!

As requested Try This    "stevebaileys@mail.com"

Regards   Steve.

smbab7203, 2021-09-09:
Hi Graham.
I have not had time to solder the new interface board yet but here are results from using the test LED.
The neg wire from LED has croc clip on it and connected to GND pin on JP7 Texas launch Board.
Using the red wire as probe these are results as best I can manage:-

From Spindle encoder to   J12.
     pin    ///////            LED On         ///////              Spinning encoder by hand Led On.

   A        /////////            no   ///////////////////////////                yes
   B        /////////            no   ////////// //////////////////               no
   I          ////// ///          yes    ///////// ///////////////////               yes
  +5v     ///////          yes   /////////// ////////////////////              yes
   GND   /////////       no   //////////////////////////////////               no

Checking J2  on Clough Interface Green connector.
 Pins//////////////// LED On.

 Plus +   ////////////    Yes
STP- /////////////    Yes
DIR- /////////////// Yes or No Depending on direction encoder is turned.
EN-  //////////////   Yes
ALM+ ///////////    Yes But Dim
ALM- ////////////     No
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
Turner75, 2021-09-10:
HI Steve
If I am reading this right;-
Out of encoder channel A, signals OK.
Out  of   "             "     B, signal no change.

Out of interface board, to motor drive, green screw terminals;-
STP  led is on continously
DIR.  Changes with direction
EN  led is on continuously.

Hmmmmm?
If the encoder output did not have both channel A & B pulsing, then the
system Board would not know the direction it was rotating and would not
change DIR output to the interface board. As I mentioned in last email, the
motor  clock pulses out of the interface, boost, board are very narrow and
depending on speed of encoder rotation may show up on led as no o/p, or dim
at fast encoder rotation, coarse threading, or led full on and dimming
slightly depending on settings in CONFIG.H file for pulse convention,
positive or negative going.
    Have you tried my suggestion of driving the motor drive unit with
interface board connections, green terminals, disconnected? That would tell
you whether or not the motor drive and motor are functional. Then if OK,
work back through the interface board checking input state to output state
on each line, after all, it's only function is to convert inputs from the
3.3 volt logic of the TI launch to the 5 volt logic required by the motor
drive unit and the display unit. Back in my younger days even 5 volt ttl
logic was considered too vulnerable to put in an industrial environmentso
we used HNIL, high noise immunity logic, 12 volt supply and lots of
capacitors and screening of inputs. How times have changed!
It would be clearer for me to give state of led as ON or OFF. Or, ON then
OFF.
Also l send via email or text, the logic states as _ an underline for zero
and -- hyphen for a one. OR, 0 (zero) 1 (one). Logic change states as
 Zero then upto a one, then down again   to zero ie, __--__  or, inverse,
--__--
     -_-_-_-_>, continuouse pulse train.
Keep at it, it's all a learning process.
Cheers Graham

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

smbab7203, 2021-09-14:
Hi Graham.
After a great deal of help and a lot of head scratching I think I have finally got the ELS working correctly and fitted on the lathe. The point of this last message is to Thank every one involved with this Git Hub project The Electronic Lead screw project.
I started watching James youTube videos and as time went on I started to get more interested and the way James explained every thing step by step, it slowly started to dawn on me I may be able to copy this and follow along and may be complete this project on my own Lathe.
To cut to the chase, I have indeed finished the ELS project and it is working.
So I would like to extend my gratefull thinks to James for all the hard work he put in in bringing this project from inception to A kit and list of parts to enable newbies like me with no electrical experience what so ever to follow along and build the project.
I must also thank Graham who spent many  hours sending me long detailed emails and instructions on how to over come my particular problems. Thank you Graham you help is much appreciated..
lastly I would like to thank you all for your different posts and questions regarding this project and all the different participents who answered these questions and posts. I have read all the posts questions and answers, you have no idea how much I have learned over the past weeks.
Thank you all.
I wish you all the best in your endevers.
Stay safe.

Kind Regards.   Steve.  UK.

Turner75, 2021-09-15:
HI
Many thanks to everyone who has participated in this project. James Clough
has been an inspiration to us all in conceiving and implementing this
project and devoting so much time and resource to bring it to fruition.
Thank you all again.
Graham T Foulkes

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

Closed 2021-09-14.

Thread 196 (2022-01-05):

No display on the Control Panel

Howard-001, 2022-01-05:
All I'm seeing on the led/button panel is the power indicator.

I've got two launchpad boards and I've tried both 1.3 & 1.4 software on each, both seem to be loading correctly in either debug or flash.

I've tries two different cables to the control board & buzzed them both to verify they're good.

I have continuity from the input connect to the appropriate pins on the display board driver.

I've checked the inputs to the adapter board, I see clocking on MOSI , constant high on DISP and open collector on CLK.

I've measured the input resistances on the adapter card, they measure ~ 560 ohms as I would expect from the schematic.

With the adapter removed from the launchpad & powering it via usb I see clocking on MOSI (J6_55) but open collector on DISP (J6_53) and CLK (J8_71).

I've doubled checked the settings foe S3 a/b, S4 & S9 and flipped them back & forth to ensure good contact.

Anyone got any ideas?  I hate to think I got two defective TI boards.

pmelevende, 2022-01-08:
I Howard,
I'm just replying as nobody else has yet - Do you have a spare display board to try? That'd be my next port of call.

Thanks
Pauly

Howard-001, 2022-01-08:
Thanks for the response Pauly, digging deeper I've found that the Q2 circuit on the interface seems to be the Root of all Evil, the +5 V that's supposed to be on the supply side of R4 wasn't there; I touched up the solder connections & I now have a high on the interface clock pins , however when plugged into either launchpad  I'm still not seeing any clock pulses, it just sits at high.

I've just ordered another interface & display as well as another launchpad , hopefully this will produce a working unit.

WheatMillington, 2022-01-13:
My experience is that the display boards are fragile and have poor QC, so hopefully that will resolve your issue.

WheatMillington, 2022-02-09:
I also managed to kill a board with sloppy desoldering.... ok two boards. My preferred solution is actually to just clip the pins very short and solder to them on the topside. You need to remove the little yellow plastic header thing, which is easy.

Howard-001, 2022-12-03:
Finally got back to this, after verifying the interce board9s) on a test bed and the display9s) with an arduino I tried a new installation of CC on a fresh machine with a fresh OS and a fresh launchpad & I've now got things displaying :)

My two other launchpad  cards still won't work :(

Chucksbp, 2022-12-03:
Sounds as though the electronics industry is also having quality issues!!

Howard-001, 2022-12-04:
From the number of others that seem to have had
the same run of "bad luck" I'm suspecting the
boards could benefit from some static suppression
measures to protect them from people with
electric personalities such as myself :)

At 12:26 PM 12/3/2022, you wrote:

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

Chucksbp, 2022-12-04:
Yes That's very possible. I'm sure that as complete electronic novices as we are, proper precautions are not taken.  I had a number 1 encoder input failure and a display board that never worked. I did after the display failure get a static pad for my bench with a wrist band but it may have been too late for the board input. Although I blame that on  the encoder?????
Luckily since the initial problems everything has been working for close to a year now, much to my enjoyment!!! the lead screw is a great addition to my old Atlas lathe! I do have a complete unit as a spare except for a motor. the board id programed and tested and ready to go!
As always thanks to James for all the effort to build and share such a wonderful piece of equipment.

Howard-001, 2022-12-04:
As embarrassing as it is I've been in electronics for 50 years :(

It's just something about me- I've got zapped
more times than I count walking into a server
room where everything is grounded & just touching a relay rack :O

God I miss vacuum tubes.

At 11:26 AM 12/4/2022, you wrote:

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

Closed 2022-12-03.

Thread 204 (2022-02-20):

Encoder connections

KennethLuscombe, 2022-02-20:
Hi.
The encoder i have has only 4 wires and a sheild  - part number (B38S-06G5-26C600B / 180744)
red
black
green
white
sheild
it looks like i need to have 5 wires - will this encoder work on the TI board

I was thinking this:
red pos
black common
green A
white B
it looks like there is one wire missing?

Please advise as to the actual connections to the TI board

KennethLuscombe, 2022-02-20:
EQEP1I maybe missing - is it needed?

Turner75, 2022-02-21:
HI Kenneth
I built the ELS, all up and running now, great! I used a Baumer encoder,
500 ppr, one of two I had to hand. I found that just the A & B quadrature
outputs worked fine, the complements -A, -B , not required,  nor is the
single pulse per rev o/p the fiducial marker pulse. My encoder is coupled,
1:2 gearing to spindle giving 1000ppr.
BTW, seems like quite a few swarf makers have had trouble with encoders
going bad. I suspect it could very well be in some cases too much side
loading on the encoder shaft. They are not built for excessive side loads
so the bearings or housing fail and the spinning photo patterned disc
generating the pulses catches the opto assembly and scrapes off the pattern.
Just my two penn'oth
Cheers Graham

On Sun, Feb 20, 2022, 6:57 AM KennethLuscombe ***@***.***>
wrote:

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

KennethLuscombe, 2022-02-21:
Thanks for the reply.
The only wires coming out of the encoder are Red Black White AND Green.

So
Does this sound correct

Red Pos
Black Neg
Yellow A
White B
Nothing connected to Z or I

The encoder is a 600ppr

so
Setup of encoder in the software 2400 ?

Thanks
Ken

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

Turner75, 2022-02-21:
HI Ken
I don't know whether the wire colour coding is standard across all rotary
encoders, unlikely. If you can't  find the connection data for this
encoder, you could try testing it out if you have some knowledge of
electronics and test equipment such as a DVM, an oscilloscope and an
adjustable bench power supply. Having said that, testing it out with just a
cheap DVM with no power on the encoder can tell you quite a lot.
    DVM (Digital Volt Meter).
 NOTE* All the following tests are done with NO power applied to the
encoder. Outputs from encoders are generally open collector, so, checking
with a meter on ohms range should give high or open circuit readings.if
your DVM has a check diode setting, then you should see a reading with the
meter leads connected one way round and open circuit in the other
direction. In contrast, the power supply inputs will usually give some
value of resistance in ohms in both directions and will vary depending upon
which way round the meter test leads are.
Hope this helps you out.
Cheers Graham

On Sun, Feb 20, 2022, 10:00 PM KennethLuscombe ***@***.***>
wrote:

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

KennethLuscombe, 2022-02-23:
The encoder is working with the 4 wires connected. Thank you

Closed 2022-02-23.

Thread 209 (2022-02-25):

Lead screw settings

KennethLuscombe, 2022-02-25:
Hi. I have tried many settings and cant seem to get it right.

I am trying to get the lead screw to turn one revolution when the chuck one revoluton. I set the dislpay to mm and the thread to 1.5

the lead screw is 1.5mm
the encoder is a 600
The setper motor is a nema 17  1.8 with encoder has a pully half the size on the steper side than one the lead screw side.

Please spell the settings out. I have tried many settings and its close but no right.

The settings i am using are :
#define LEADSCREW_HMM 150
#define STEPPER_MICROSTEPS 28 ( I have tried from 2 - 28 and 26 - 28 is close)
#define STEPPER_RESOLUTION 200
#define ENCODER_RESOLUTION 2400
I have changed nothing else
also how do i make it start up in mm not inch

Please help

KennethLuscombe, 2022-02-25:
using software version 14

KennethLuscombe, 2022-02-25:
As per the above I have just tried

stepper resolution 1000
stepper micro step 2

I then get 3 revolutions of chuck to one on lead screw.

KennethLuscombe, 2022-02-25:
if I change the encoder to #define ENCODER_RESOLUTION 600 all is well except the RPM is on display only show 1/4 the actual RPM

Chucksbp, 2022-02-25:
I would say the lead screw is correct at 150hmm, the encoder resolution looks correct at 2,400 assuming your encoder is operating at a 1 to 1 ratio. What is your stepper motor switches set to. Its best to set it a 1,000 and then your resolution would be set to 1,000 and the micro steps should also be set a 2 for a 2 to 1 ratio.
One thing I found out during my installation is all pulleys are not the same size. I had two 60 tooth pulleys of different brands driving my encoder one was a bit larger diameter and although they were both 60 tooth they would get out of sink very quickly. Even the same brand cheap Chinese ones will be off from one batch to another. I finally found two very close and took .003 off the diameter to make a matched set and i haven't had an issue.  Put a mark on both the encoder and drive pulley and run it for a few minutes and see if the marks are still in sync. Also belt tension seems to play a roll on the encoder

KennethLuscombe, 2022-02-25:
I feel silly . Thank you so much. I missed the fact that i could set things up on the stepper driver. I had it set to 8000 so 1000 sorted it out.  It is working so perfectly now. Thank you so much.

and thank you Clough for building such a nice product.

Closed 2022-02-25.

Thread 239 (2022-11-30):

Resolving encoder not working with 5 volt supply

dlmock99, 2022-11-30:
Found that my encoder would work at supply voltages higher than 5 volts but not with 5 volts.  The problem is with the internal voltage regulator in the encoder a LM78M05.  Quick fix is to remove the regulator and solder a jumper from the input and output board pads.  The fix is good only if you are using 5 volts to power the encoder.  BTW the encoder is the Omron E6B2-CWZ6C the same as James had listed.  Yes it's speced. to work at 5 to 35 volts.  Guess it depends on which company manufactures the voltage regulator.

kwackers, 2022-12-01:
Is it a genuine Omron or a copy?
78 series regulators require the input voltage to be around 2v higher than the output to do anything so it doesn't make sense to claim a 5v supply (superficially at least).

dlmock99, 2022-12-01:
It's the real deal.  I agree with you that the supply voltage should be higher that the regulated output.  The encoder came with the data sheet and it specs. that the supply voltage is to be 5 to 24 volt DC . Yet at 5 volts there was no output.  Removing the regulator and adding a jumper will get it working.
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

Closed 2022-12-01.

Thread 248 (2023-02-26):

36 vs 48 volt power supply?

javaduke, 2023-02-26:
I'm a bit confused, I ordered the servo that James suggested, and it says 24-36 Volt, but the power supply is 48 volt - so is it ok to power the servo with 48 volt instead of 36, or should I get the 36 volt power supply?

tomvikse, 2023-02-26:
48V no problem..
https://youtu.be/clgpZJFoqIQ?list=PLDlWKv7KIIr90ZZ7Zqt-ge5nVVdS3WVgg&t=150

javaduke, 2023-02-27:
OK, thanks, hopefully it won't burn down :) It is confusing though, the product description on StepperOnline says 20-50VDC, the label on the integrated controller says 24-36V and the power supply is 48V...

johnsonm, 2023-04-08:
I note that James had his first servo die, and 48V is close to the rated maximum; that's not a lot of headroom for transients, say from back-EMF. The servo's rated torque is at 36V, so it's not crazy to run it on 36V, with more headroom.

I will be running my servo at 36V for this reason, and if I swap out for 48V due to insufficient torque, I'll plan either to adjust the nominal 48V supply a few volts lower, or to add transient protection; at least a large-value capacitor, and maybe a crowbar shunt to avoid exceeding 49V. But I don't expect that to be necessary.

tomvikse, 2023-04-08:
Using a 48v power supply adjusted down to 42v.. good for 2 years now..

Closed 2023-02-27.

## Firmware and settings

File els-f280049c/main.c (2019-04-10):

//
// Included Files
//
#include "F28x_Project.h"     // Device Headerfile and Examples Include File
#include "ControlPanel.h"
#include "StepperDrive.h"
#include "Encoder.h"
#include "Configuration.h"
#include <stdio.h>

//
// Function Prototypes statements for functions found within this file.
//
__interrupt void cpu_timer0_isr(void);

long double feed = 200.0 * 8.0 / 4096.0;
//Uint32 numerator = (Uint32)250 * 10 * 12 * 200 * 8;
//Uint32 denominator = (Uint32)4096 * 254 * 100;

//
// Main
//
void main(void)
{
#ifdef _FLASH
    // Copy time critical code and Flash setup code to RAM
    // The RamfuncsLoadStart, RamfuncsLoadEnd, and RamfuncsRunStart
    // symbols are created by the linker. Refer to the linker files.
    memcpy(&RamfuncsRunStart, &RamfuncsLoadStart, (size_t)&RamfuncsLoadSize);

    // Initialize the flash instruction fetch pipeline
    // This configures the MCU to pre-fetch instructions from flash.
    InitFlash();
#endif

    //
    // Step 1. Initialize System Control:
    // PLL, WatchDog, enable Peripheral Clocks
    // This example function is found in the F2806x_SysCtrl.c file.
    //
    InitSysCtrl();

    //
    // Step 2. Initalize GPIO:
    // This example function is found in the F2806x_Gpio.c file and
    // illustrates how to set the GPIO to it's default state.
    //
    // InitGpio();  // Skipped for this example

    //
    // Step 3. Clear all interrupts and initialize PIE vector table:
    // Disable CPU interrupts
    //
    DINT;

    //
    // Initialize the PIE control registers to their default state.
    // The default state is all PIE interrupts disabled and flags
    // are cleared.
    // This function is found in the F2806x_PieCtrl.c file.
    //
    InitPieCtrl();

    //
    // Disable CPU interrupts and clear all CPU interrupt flags
    //
    IER = 0x0000;
    IFR = 0x0000;

    //
    // Initialize the PIE vector table with pointers to the shell Interrupt
    // Service Routines (ISR).
    // This will populate the entire table, even if the interrupt
    // is not used in this example.  This is useful for debug purposes.
    // The shell ISR routines are found in F2806x_DefaultIsr.c.
    // This function is found in F2806x_PieVect.c.
    //
    InitPieVectTable();

    //
    // Interrupts that are used in this example are re-mapped to
    // ISR functions found within this file.
    //
    EALLOW;    // This is needed to write to EALLOW protected registers
    PieVectTable.TIMER0_INT = &cpu_timer0_isr;
    EDIS;      // This is needed to disable write to EALLOW protected registers

    //
    // Step 4. Initialize the Device Peripheral. This function can be
    //         found in F2806x_CpuTimers.c
    //
    InitCpuTimers();   // For this example, only initialize the Cpu Timers

    //
    // Configure CPU-Timer 0 to interrupt every 500 milliseconds:
    // 80MHz CPU Freq, 50 millisecond Period (in uSeconds)
    //
    ConfigCpuTimer(&CpuTimer0, 90, STEPPER_CYCLE_US);

    //
    // To ensure precise timing, use write-only instructions to write to the
    // entire register. Therefore, if any of the configuration bits are changed
    // in ConfigCpuTimer and InitCpuTimers (in F2806x_CpuTimers.h), the
    // below settings must also be updated.
    //

    //
    // Use write-only instruction to set TSS bit = 0
    //
    CpuTimer0Regs.TCR.all = 0x4001;

    //
    // Set up SPI for control panel
    //
    ControlPanel_Init();

    //
    // Set up GPIO and state machine for stepper drive
    //
    StepperDrive_Init();

    //
    // Set up Encoder input
    //
    Encoder_Init();

    // GPIO 9 as an indicator
    EALLOW;
    GpioCtrlRegs.GPAMUX1.bit.GPIO7 = 0;
    GpioCtrlRegs.GPADIR.bit.GPIO7 = 1;
    GpioDataRegs.GPACLEAR.bit.GPIO7 = 1;
    GpioCtrlRegs.GPAMUX1.bit.GPIO2 = 0;
    GpioCtrlRegs.GPADIR.bit.GPIO2 = 1;
    GpioDataRegs.GPACLEAR.bit.GPIO2 = 1;
    EDIS;

    //
    // Step 5. User specific code, enable interrupts:
    //

    //
    // Enable CPU INT1 which is connected to CPU-Timer 0
    //
    IER |= M_INT1;

    //
    // Enable TINT0 in the PIE: Group 1 interrupt 7
    //
    PieCtrlRegs.PIEIER1.bit.INTx7 = 1;

    //
    // Enable global Interrupts and higher priority real-time debug events
    //
    EINT;   // Enable Global interrupt INTM
    ERTM;   // Enable Global realtime interrupt DBGM

    //
    // Start up
    //

    //
    // Step 6. IDLE loop. Just sit and loop forever (optional)
    //
    union KEY_REG keys;
    keys.all = 0xff;

    for(;;) {
        ControlPanel_SetLEDs(keys.all);
        ControlPanel_SetValue(feed);

        keys = ControlPanel_Refresh();

        //
        // Respond to keypresses
        //
        if( keys.all & 0x01 ) {
            StepperDrive_SetDesiredPosition(4);
            feed += 0.001;
        }
        if( keys.all & 0x02 ) {
            StepperDrive_SetDesiredPosition(3);
        }
        if( keys.all & 0x04 ) {
            StepperDrive_SetDesiredPosition(2);
        }
        if( keys.all & 0x08 ) {
            StepperDrive_SetDesiredPosition(1);
            feed -= 0.001;
        }
        if( keys.all & 0x10 ) {
            StepperDrive_SetDesiredPosition(0);
        }
        if( keys.all & 0x20 ) {
            StepperDrive_SetDesiredPosition(-1);
        }
        if( keys.all & 0x40 ) {
            StepperDrive_SetDesiredPosition(-2);
        }
        if( keys.all & 0x80 ) {
            StepperDrive_SetDesiredPosition(-3);
        }

        if( feed > 0.999 ) feed = 0.999;
        if( feed < 0.0 ) feed = 0.0;

        DELAY_US(10000); // update at 100Hz-ish

    };
}


Uint32 previousSpindlePosition = 0;
long double previousFeed = 0;


inline int32 Apply_Ratio(Uint32 count)
{
    //return ((long long)count) * numerator / denominator;
    return count * feed;
}

//
// cpu_timer0_isr -
//
__interrupt void
cpu_timer0_isr(void)
{
    CpuTimer0.InterruptCount++;

    // flag entrance to ISR for timing
    GpioDataRegs.GPASET.bit.GPIO7 = 1;

    //
    // Calculate the correct stepper position
    //
    Uint32 spindlePosition = Encoder_GetPosition();
    int32 desiredSteps = Apply_Ratio(spindlePosition);

    // overflow
    if( spindlePosition < previousSpindlePosition && previousSpindlePosition - spindlePosition > Encoder_GetMaxCount()/2 ) {
        StepperDrive_IncrementCurrentPosition(-1 * Apply_Ratio(Encoder_GetMaxCount()));
    }
    // underflow
    if( spindlePosition > previousSpindlePosition && spindlePosition - previousSpindlePosition > Encoder_GetMaxCount()/2 ) {
        StepperDrive_IncrementCurrentPosition(Apply_Ratio(Encoder_GetMaxCount()));
    }

    StepperDrive_SetDesiredPosition(desiredSteps);

    // if the feed changed, we want to reset and avoid a big step
    if( feed != previousFeed ) {
        StepperDrive_SetCurrentPosition(desiredSteps);
    }

    previousSpindlePosition = spindlePosition;
    previousFeed = feed;

    //
    // Service the stepper driver
    //
    StepperDrive_Service_ISR();

    ControlPanel_SetRPM(Encoder_GetRPM());

    // flag exit from ISR for timing
    GpioDataRegs.GPACLEAR.bit.GPIO7 = 1;

    //
    // Acknowledge this interrupt to receive more interrupts from group 1
    //
    PieCtrlRegs.PIEACK.all = PIEACK_GROUP1;
}

//
// End of File
//

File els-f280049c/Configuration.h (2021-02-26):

// Clough42 Electronic Leadscrew
// https://github.com/clough42/electronic-leadscrew
//
// MIT License
//
// Copyright (c) 2019 James Clough
//
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

#ifndef __CONFIGURATION_H
#define __CONFIGURATION_H




//================================================================================
//                                  LEADSCREW
//
// Define the type and pitch of leadscrew you have in your lathe.  If you have an
// imperial leadscrew, define LEADSCREW_TPI.  If you have a metric leadscrew,
// define LEADSCREW_HMM (pitch in hundredths of a millimeter).  Do not define
// both.
//================================================================================

// For Imperial leadscrews: pitch in Threads Per Inch (TPI)
#define LEADSCREW_TPI 12

// For metric leadscrews: pitch in hundredths of a millimeter (HMM)
// Example: 200hmm = 2mm
//#define LEADSCREW_HMM 200




//================================================================================
//                                STEPPER/SERVO
//
// Define the number of steps and microsteps for your stepper motor, the pin
// polarity of the driver, and whether to use additional features, like servo
// alarm feedback.
//
// NOTE: If you are using a servo drive with something other than a 1:1 drive
// ratio, you can use the STEPPER_MICROSTEPS to compensate.  For example, if you
// have a servo configured for 1000 steps/revolution and it drives the leadscrew
// through a 3:1 reduction, you can set STEPPER_RESOLUTION to 1000 and
// STEPPER_MICROSTEPS to 3.
//================================================================================

// Steps and microsteps
#define STEPPER_MICROSTEPS 8
#define STEPPER_RESOLUTION 200

// Separate step and microstep settings for feed rates.  Redefine these if your
// lathe has a separate feed drive train with a different ratio.
#define STEPPER_MICROSTEPS_FEED STEPPER_MICROSTEPS
#define STEPPER_RESOLUTION_FEED STEPPER_RESOLUTION

// Step, direction and enable pins are normally active-high
// #define INVERT_STEP_PIN true
// #define INVERT_DIRECTION_PIN true
#define INVERT_ENABLE_PIN true
#define INVERT_ALARM_PIN true

// Enable servo alarm feedback
#define USE_ALARM_PIN




//================================================================================
//                                 ENCODER
//
// Define the type of encoder you are using on the spindle.  The firmware assumes
// the encoder is turning at a 1:1 ratio with the spindle.
//
// NOTE: the firmware is concerned with the quadrature edge count, which is
// four times the number of pulses.  For example, if you have a 1024 P/R
// encoder, you need to enter 4096 here.
//================================================================================

// Encoder resolution (counts per revolution)
#define ENCODER_RESOLUTION 4096

// Which encoder input to use
#define ENCODER_USE_EQEP1
//#define ENCODER_USE_EQEP2




//================================================================================
//                               CALCULATIONS
//
// Define how calculations should be performed.  Most users will not need to
// touch these settings.
//================================================================================

// Use floating-point math for gear ratios
#define USE_FLOATING_POINT




//================================================================================
//                                HARDWARE
//
// Define which hardware you're using:
//
//  1 - LaunchXL F280049C with ELS BoostXL v1
//  2 - LaunchXL F280049C with ELS BoostXL v2
//================================================================================

// See hardware version table above
#define HARDWARE_VERSION 2




//================================================================================
//                                FEATURES
//
// Additional features that can be enabled for your configuration.
//================================================================================

// Ignore all key presses when the machine is running.  Normally, only the mode
// and direction keys are ignored.
//#define IGNORE_ALL_KEYS_WHEN_RUNNING




//================================================================================
//                              VALIDATION/TRIP
//
// Validation thresholds and automatic trip behavior.
//================================================================================

// Maximum number of buffered steps
// The ELS can only output steps at approximately 100KHz.  If you ask the ELS to
// output steps faster than this, it will get behind and will stop automatically
// when the buffered step count exceeds this value.
#define MAX_BUFFERED_STEPS 100
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

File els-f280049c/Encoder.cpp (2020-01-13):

// Clough42 Electronic Leadscrew
// https://github.com/clough42/electronic-leadscrew
//
// MIT License
//
// Copyright (c) 2019 James Clough
//
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

#include "Encoder.h"
#include "Configuration.h"


Encoder :: Encoder( void )
{
    this->previous = 0;
    this->rpm = 0;
}

void Encoder :: initHardware(void)
{
    EALLOW;

#ifdef ENCODER_USE_EQEP1
    GpioCtrlRegs.GPBPUD.bit.GPIO35 = 0;     // Enable pull-up on GPIO35 (EQEP1A)
    GpioCtrlRegs.GPBPUD.bit.GPIO37 = 0;     // Enable pull-up on GPIO371 (EQEP1B)
    GpioCtrlRegs.GPBPUD.bit.GPIO59 = 0;     // Enable pull-up on GPIO59 (EQEP1I)

    GpioCtrlRegs.GPBQSEL1.bit.GPIO35 = 0;   // Sync to SYSCLKOUT GPIO35 (EQEP1A)
    GpioCtrlRegs.GPBQSEL1.bit.GPIO37 = 0;   // Sync to SYSCLKOUT GPIO37 (EQEP1B)
    GpioCtrlRegs.GPBQSEL2.bit.GPIO59 = 0;   // Sync to SYSCLKOUT GPIO59 (EQEP1I)

    GpioCtrlRegs.GPBMUX1.bit.GPIO35 = 1;    // Configure GPIO35 as EQEP1A
    GpioCtrlRegs.GPBGMUX1.bit.GPIO35 = 2;
    GpioCtrlRegs.GPBMUX1.bit.GPIO37 = 1;    // Configure GPIO37 as EQEP1B
    GpioCtrlRegs.GPBGMUX1.bit.GPIO37 = 2;
    GpioCtrlRegs.GPBMUX2.bit.GPIO59 = 3;    // Configure GPIO59 as EQEP1I
    GpioCtrlRegs.GPBGMUX2.bit.GPIO59 = 2;
#endif
#ifdef ENCODER_USE_EQEP2
    GpioCtrlRegs.GPAPUD.bit.GPIO14 = 0;     // Enable pull-up on GPIO14 (EQEP2A)
    GpioCtrlRegs.GPAPUD.bit.GPIO15 = 0;     // Enable pull-up on GPIO15 (EQEP2B)
    GpioCtrlRegs.GPAPUD.bit.GPIO26 = 0;     // Enable pull-up on GPIO26 (EQEP2I)

    GpioCtrlRegs.GPAQSEL1.bit.GPIO14 = 0;   // Sync to SYSCLKOUT GPIO14 (EQEP2A)
    GpioCtrlRegs.GPAQSEL1.bit.GPIO15 = 0;   // Sync to SYSCLKOUT GPIO15 (EQEP2B)
    GpioCtrlRegs.GPAQSEL2.bit.GPIO26 = 0;   // Sync to SYSCLKOUT GPIO26 (EQEP2I)

    GpioCtrlRegs.GPAMUX1.bit.GPIO14 = 2;    // Configure GPIO14 as EQEP2A
    GpioCtrlRegs.GPAGMUX1.bit.GPIO14 = 2;
    GpioCtrlRegs.GPAMUX1.bit.GPIO15 = 2;    // Configure GPIO15 as EQEP2B
    GpioCtrlRegs.GPAGMUX1.bit.GPIO15 = 2;
    GpioCtrlRegs.GPAMUX2.bit.GPIO26 = 2;    // Configure GPIO26 as EQEP2I
    GpioCtrlRegs.GPAGMUX2.bit.GPIO26 = 0;
#endif

    EDIS;

    ENCODER_REGS.QDECCTL.bit.QSRC = 0;         // QEP quadrature count mode
    ENCODER_REGS.QDECCTL.bit.IGATE = 1;        // gate the index pin
    ENCODER_REGS.QDECCTL.bit.QAP = 1;          // invert A input
    ENCODER_REGS.QDECCTL.bit.QBP = 1;          // invert B input
    ENCODER_REGS.QDECCTL.bit.QIP = 1;          // invert index input
    ENCODER_REGS.QEPCTL.bit.FREE_SOFT = 2;     // unaffected by emulation suspend
    ENCODER_REGS.QEPCTL.bit.PCRM = 1;          // position count reset on maximum position
    ENCODER_REGS.QPOSMAX = _ENCODER_MAX_COUNT;  // Max position count

    ENCODER_REGS.QUPRD = CPU_CLOCK_HZ / RPM_CALC_RATE_HZ; // Unit Timer latch at RPM_CALC_RATE_HZ Hz
    ENCODER_REGS.QEPCTL.bit.UTE=1;             // Unit Timeout Enable
    ENCODER_REGS.QEPCTL.bit.QCLM=1;            // Latch on unit time out

    ENCODER_REGS.QEPCTL.bit.QPEN=1;            // QEP enable

}

Uint16 Encoder :: getRPM(void)
{
    if(ENCODER_REGS.QFLG.bit.UTO==1)       // If unit timeout (one 10Hz period)
    {
        Uint32 current = ENCODER_REGS.QPOSLAT;
        Uint32 count = (current > previous) ? current - previous : previous - current;

        // deal with over/underflow
        if( count > _ENCODER_MAX_COUNT/2 ) {
            count = _ENCODER_MAX_COUNT - count; // just subtract from max value
        }

        rpm = count * 60 * RPM_CALC_RATE_HZ / ENCODER_RESOLUTION;

        previous = current;
        ENCODER_REGS.QCLR.bit.UTO=1;       // Clear interrupt flag
    }

    return rpm;
}

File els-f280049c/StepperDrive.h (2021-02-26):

// Clough42 Electronic Leadscrew
// https://github.com/clough42/electronic-leadscrew
//
// MIT License
//
// Copyright (c) 2019 James Clough
//
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

#ifndef __STEPPERDRIVE_H
#define __STEPPERDRIVE_H

#include "F28x_Project.h"
#include "Configuration.h"


#define STEP_PIN GPIO0
#define DIRECTION_PIN GPIO1
#define ENABLE_PIN GPIO6
#define ALARM_PIN GPIO7

#define GPIO_SET(pin) GpioDataRegs.GPASET.bit.pin = 1
#define GPIO_CLEAR(pin) GpioDataRegs.GPACLEAR.bit.pin = 1
#define GPIO_GET(pin) GpioDataRegs.GPADAT.bit.pin

#ifdef INVERT_STEP_PIN
#define GPIO_SET_STEP GPIO_CLEAR(STEP_PIN)
#define GPIO_CLEAR_STEP GPIO_SET(STEP_PIN)
#else
#define GPIO_SET_STEP GPIO_SET(STEP_PIN)
#define GPIO_CLEAR_STEP GPIO_CLEAR(STEP_PIN)
#endif

#ifdef INVERT_DIRECTION_PIN
#define GPIO_SET_DIRECTION GPIO_CLEAR(DIRECTION_PIN)
#define GPIO_CLEAR_DIRECTION GPIO_SET(DIRECTION_PIN)
#else
#define GPIO_SET_DIRECTION GPIO_SET(DIRECTION_PIN)
#define GPIO_CLEAR_DIRECTION GPIO_CLEAR(DIRECTION_PIN)
#endif

#ifdef INVERT_ENABLE_PIN
#define GPIO_SET_ENABLE GPIO_CLEAR(ENABLE_PIN)
#define GPIO_CLEAR_ENABLE GPIO_SET(ENABLE_PIN)
#else
#define GPIO_SET_ENABLE GPIO_SET(ENABLE_PIN)
#define GPIO_CLEAR_ENABLE GPIO_CLEAR(ENABLE_PIN)
#endif

#ifdef INVERT_ALARM_PIN
#define GPIO_GET_ALARM (GPIO_GET(ALARM_PIN) == 0)
#else
#define GPIO_GET_ALARM (GPIO_GET(ALARM_PIN) != 0)
#endif


class StepperDrive
{
private:
    //
    // Current position of the motor, in steps
    //
    int32 currentPosition;

    //
    // Desired position of the motor, in steps
    //
    int32 desiredPosition;

    //
    // current state-machine state
    // bit 0 - step signal
    // bit 1 - direction signal
    //
    Uint16 state;

    //
    // Is the drive enabled?
    //
    bool enabled;

public:
    StepperDrive();
    void initHardware(void);

    void setDesiredPosition(int32 steps);
    void incrementCurrentPosition(int32 increment);
    void setCurrentPosition(int32 position);

    bool checkStepBacklog();

    void setEnabled(bool);

    bool isAlarm();

    void ISR(void);
};

inline void StepperDrive :: setDesiredPosition(int32 steps)
{
    this->desiredPosition = steps;
}

inline void StepperDrive :: incrementCurrentPosition(int32 increment)
{
    this->currentPosition += increment;
}

inline void StepperDrive :: setCurrentPosition(int32 position)
{
    this->currentPosition = position;
}

inline bool StepperDrive :: checkStepBacklog()
{
    if( abs(this->desiredPosition - this->currentPosition) > MAX_BUFFERED_STEPS ) {
        setEnabled(false);
        return true;
    }
    return false;
}

inline void StepperDrive :: setEnabled(bool enabled)
{
    this->enabled = enabled;
    if( this->enabled ) {
        GPIO_SET_ENABLE;
    }
    else
    {
        GPIO_CLEAR_ENABLE;
    }
}

inline bool StepperDrive :: isAlarm()
{
#ifdef USE_ALARM_PIN
    return GPIO_GET_ALARM;
#else
    return false;
#endif
}


inline void StepperDrive :: ISR(void)
{
    if(enabled) {

        switch( this->state ) {

        case 0:
            // Step = 0; Dir = 0
            if( this->desiredPosition < this->currentPosition ) {
                GPIO_SET_STEP;
                this->state = 2;
            }
            else if( this->desiredPosition > this->currentPosition ) {
                GPIO_SET_DIRECTION;
                this->state = 1;
            }
            break;

        case 1:
            // Step = 0; Dir = 1
            if( this->desiredPosition > this->currentPosition ) {
                GPIO_SET_STEP;
                this->state = 3;
            }
            else if( this->desiredPosition < this->currentPosition ) {
                GPIO_CLEAR_DIRECTION;
                this->state = 0;
            }
            break;

        case 2:
            // Step = 1; Dir = 0
            GPIO_CLEAR_STEP;
            this->currentPosition--;
            this->state = 0;
            break;

        case 3:
            // Step = 1; Dir = 1
            GPIO_CLEAR_STEP;
            this->currentPosition++;
            this->state = 1;
            break;
        }

    } else {
        // not enabled; just keep current position in sync
        this->currentPosition = this->desiredPosition;
    }
}

#endif // __STEPPERDRIVE_H

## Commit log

2019-03-22 Initial prototype code.
2019-03-22 Clean up stepper enable.
2019-03-22 Prototype control panel structures.
2019-03-23 Refactor control panel. Add Encoder support. Add RPM calculation and display.
2019-03-23 Invert encoder inputs #define RPM update frequency Remove leading zeroes from RPM readout
    [ControlPanel.c, Encoder.c, main.c]
2019-03-23 Drive stepper for testing. Caution: now underflow handling.
2019-03-24 Add overflow/underflow handling for stepper. Switch to double-precision floats for feed rates. Introduce Configuration.h for config parameters.
    [Configuration.h]
2019-03-24 Declare ENCODER_MAX_COUNT to be internal and access it with an inline function.
2019-04-09 Initial port to F28049x. Compiling, but not working.
    [Configuration.h]
2019-04-09 Update LED registers.
2019-04-09 Add macros for set/clear on chip-select pin.
2019-04-11 Make CPU frequency a configurable item.
    [Configuration.h]
2019-04-11 Add thread and feed tables.
2019-04-12 Partial C++ conversion
    [Configuration.h]
2019-04-12 Fix CPU clock config. Add some comments.
    [Configuration.h]
2019-04-12 Plumb reverse flag through to stepper driver
    [Core.cpp, StepperDrive.cpp, StepperDrive.h]
2019-04-12 Remove original els-firmware prototype
    [Configuration.h]
2019-04-12 Clean up comments and add license to source files
    [Configuration.h]
2019-04-12 Add config item for UI refresh rate. Increase step rate.
    [Configuration.h]
2019-04-12 Make leadscrew, stepper and encoder parameters configurable.
    [Configuration.h]
2019-04-13 Add floating-point calculation mode
    [Configuration.h]
2019-04-19 Add configuration items to invert pins.
    [Configuration.h]
2019-04-23 Fix timing issue with TM1638 CS (STB) line.
    [ControlPanel.cpp]
2019-06-05 Remove encoder resolution magic number
    Commit 9e4f611 made encoder resolution a configurable parameter, however
    the original "magic number" was not removed from the Encoder::getRPM
    function. This creates a regression bug if the encoder resolution is
    configured to anything other than 4096
    [Encoder.cpp]
2019-08-12 Add infrastructure to read servo alarm pin.
    [Configuration.h]
2019-08-24 Add EEPROM support (#9)
    * Add basic EEPROM infrastructure.
    * Extract common SPI Bus out of ControlPanel and EEPROM.
    * EEPROM read/write cycle working
2019-08-24 Add support for metric leadscrews. Add sanity checks. (#11)
    [Configuration.h]
2019-09-01 Fix metric leadcrew calculation error. (#14)
    [Tables.cpp]
2019-09-08 Create experimental encoder simulator.
2019-09-08 Drive encoder simulator from a table lookup.
2019-11-30 Add support for ELS Boost V2 (#19)
    * Fix 8-bit SPI mode for EEPROM.
    * Add support for V2 EEPROM.
    * Add test fixture project.
    * Build test fixture
    * Test key inputs and drive Larson scanner.
    * Add 8K EEPROM testing.
    * Fix comment.
    * VREG test working on A5
    * VREG test now working on Analog in B1.
    * Finish test fixture.
    Add stepper and alarm pin tests
    Allow EEPROMs larger than 8K
    Loosen VREG constraint to allow for unreliable pogo resistance
    * Simplified test code.
    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
    [Configuration.h]
2019-11-30 Incorporate #29 from carneeki: added two BSP threads, made 11.5 actually 11.5 (#32)
    * added two BSP threads, made 11.5 actually 11.5
    * Merge branch 'master' of
    https://github.com/carneeki/electronic-leadscrew into carneeki-master
    Fix ram link file to allow for larger thread tables.
    # Please enter a commit message to explain why this merge is necessary,
    # especially if it merges an updated upstream into a topic branch.
    #
    # Lines starting with '#' will be ignored, and an empty message aborts
    # the commit.
    [Tables.cpp]
2019-12-01 Add additional comments to Configuration.h
    [Configuration.h]
2020-01-13 Add configuration to use second encoder (EQEP2) (#46)
    * Add setting to use second encoder.
    * Got EQEP2 working. Rolled version number.
    [Configuration.h]
2020-10-05 Fix overflow caused by large metric threads. Suggested by hugosman65 (PR#77)
    [Tables.cpp]
2020-10-05 Slow down SPI bus (from 250Kbps to 98Kbps) to make it more noise-immune.
    [SPIBus.cpp]
2020-10-06 Increase SPI timing delays slightly to make communication more robust.
2020-10-06 Aggressively filter bad key input: require multiple consecutive reads, validate only one key is pressed, require all keys to be released beteween valid actions.
2020-10-06 Do not allow changes to feed/thread, metric/imperial, forward/reverse, or settings when the machine is running.
2020-10-06 Add configuration option to ignore all keypresses (including up/down) when the machine is running..
    [Configuration.h]
2020-10-10 Make power button disable stepper drive and turn off control panel.
2020-10-10 Make power button disable stepper drive and turn off control panel. (#93)
2020-10-10 Revert "Make power button disable stepper drive and turn off control panel. (#93)"
    This reverts commit c956b266686502443c96946314fa9c63c52522b9.
    [Core.cpp, StepperDrive.h]
2020-10-10 Manual merge of travistabbal's different stepper rates for feed and threading. (#95)
    [Configuration.h]
2020-10-10 Fix startup initialization so the stepper/servo will actually run.
2020-10-11 Change tachometer update to twice per second to reduce jitter. (#96)
    [Configuration.h]
2021-02-25 Panic stop with error message if stepper output backlog exceeds a configured value.
    [Configuration.h]
2022-10-27 Add integrated servo wiring diagram
2022-11-29 Switch to graphic of easy servo
2022-11-29 Add Easy Servo Motor image
2022-11-29 Add 200 icon for Easy Servo Motor
2024-08-01 Create LaunchPad DIN Rail Mount.stl
    [LaunchPad DIN Rail Mount.stl]
2024-10-13 New LED and Key continuity image
